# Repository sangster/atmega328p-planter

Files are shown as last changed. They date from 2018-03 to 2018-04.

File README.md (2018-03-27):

# Planter

This project manages the water and light cycles of a single houseplant.

This was a learning exercise to begin teaching myself embedded development. I
wouldn't recommend you use this code for anything you deem to be important.

For the sake of code-cleanliness, non-application code has been extracted to a
helper library:
[embedded-sangster_atmega328p](https://github.com/sangster/embedded-sangster_atmega328p).

## Features

 - An LCD screen which shows live statistics: Soil moisture, air humidity, air
   temperature, and the current date and time.
 - To save power, the LCD turns off 1 minute after the user stops pressing
   buttons.
 - A menu system which allows the user to change the runtime settings of the
   system (detailed below), using the four general-purpose buttons below the LCD
   screen.
 - Automatically waters the plant on a given schedule, but only if the soil
   moisture falls below a certain percentage.
 - An audible alarm system to notify you when the water tank runs low. This
   also disables the pump so it doesn't "run dry."
 - A toggle switch on the front panel to disable the audible alarm, in case it
   gets annoying.
 - Automatically turns on/off a grow light on a given schedule.
 - Supports an optional microSD card. If present, various spreadsheets will be
   populated over time. Hopefully, this data can be used to fine-tune your
   plant's care.

### Menu

The menu provides the following functionality and configuration options:

 - **Water Plant!**: Runs the watering process, regardless of the schedule or
   current soil moisture.
 - **Toggle Lamp**: Switches the lamp on/off, regardless of the current
   schedule. This "override" will continue until the next scheduled event. ex:
   If the lamp is scheduled to turn on at 8:00 am. If you toggle it off at 8:05
   am, it will remain off until 8:00 am the following day.
 - **Date Config**: Set the current year, month, and day.
 - **Time Config**: Set the current hour (24h clock) and minute.
 - **Lamp Config**:
   - **Starting hour**: The hour of the day the lamp should turn on.
   - **Period**: The number of hours the lamp should remain on.
 - **Pump Config**:
   - **Moisture Trigger**: The level of soil moisture (%) below which the pump
     will be allowed to run.
   - **Delay**: The minimum amount of time that must pass after watering the
     plant before watering it again.
   - **Amount**: The amount of water (mL) to water the plant with each time.
 - **Log Config**:
   - **Period**: How often general statistics will be written to the SD card
     (if one is available)

### Log Files

If the optional SD card is inserted, three types of log files (in the form of
.csv spreadsheets) will be populated over time.

#### General Statistics

Every so often (See the menu option **Log Config > Period**), the Planter will
dump all the statistics it has available to a log file. As this file will be
updated most often and has the most columns, a new file will be created each
month, with the filename format of `YYYY-MM.log`.

##### Example

| Time | Moisture (%) | Humidity (%) | Temperature (C) | Time of Last Watering | Conf: Lamp Start | Conf: Lamp Period (Hrs) | Conf: Pump Minimum (% Moisture) | Conf: Pump Delay (Hrs) | Conf: Pump Amount (mL) | Conf: Log Period (Mins) | Lamp State | Buoy State |
| --- | --- | --- | --- | --- | --- | --- | --- | --- | --- | --- | --- | --- |
| 2018-03-22 10:00:00 | 90 | 20 | 21 | 2018-03-21 20:31:59 | 08:00 | 10 | 20 | 4 | 50 | 6 | Off | Up |
| 2018-03-22 11:00:01 | 86 | 20 | 22 | 2018-03-21 20:31:59 | 08:00 | 10 | 20 | 4 | 50 | 6 | On | Up |

#### Watering History

Every time the plant gets watered a new entry is added to the `Water.log`
spreadsheet, including the soil moisture (%) before the plant was watered and
how much water was supplied.

##### Example

| Time | Moisture Before | mL |
| --- | --- | --- |
| 2018-03-12 00:12:17 | 19 | 52 |
| 2018-03-15 15:15:31 | 17 | 50 |

#### Watering History

Every time the grow light is turned on or off, the event is recorded in the
`Lamp.log` spreadsheet.

##### Example

| Time | New Lamp State |
| --- | --- |
| 2018-03-18 00:08:00 | On  |
| 2018-03-18 00:18:00 | Off |
| 2018-03-19 00:09:00 | On  |

## Build Process

### Major Components

  - Two custom PCBs (more info below):
    - Motherboard
    - UI panel
  - Generic 2x16 LCD panel
  - 4 momentary push buttons
  - 1 toggle switch
  - OSEPP Humidity & Moisture Breakout (MHUM-01)
  - OSEPP Real-time Clock & microSD Breakout (RTCSD-01)
  - Generic YF-S402 Water Flow Sensor
  - Water Level Sensor Vertical Float Switch
  - The cheapest, weakest DC acquarium pump you can find
  - A cheapo desk lamp, with a "grow" lightbulb
  - 12v/2amp AC adapter
  - 12cm x 12cm x 9cm plastic project box
  - A plastic container to act as the water resevoir

### Custom PCBs

This project uses 2 homemade PCBs to wire everything together:

 - The Motherboard
 - The UI panel daughterboard

Both were designed using the open-source [Fritzing](http://fritzing.org), then
etched onto copper clad using the "toner transfer" process.

#### Motherboard

The motherboard's responsibilities are:

 - Receive 12v from the AC adapter.
 - Step the power down to 5v for the MCU and various low voltage components.
 - Provide 12v to the pump (when active).
 - Switch the Lamp and Pump relays.
 - Provide headers to connect the UI panel and other peripheral components.

##### Files

 - [mainboard.fzz](./planning/mainboard.fzz): The Fritzing file used to design
   the PCB and print out the toner-transfer sheets.
 - [mainboard.pdf](./toner-transfers/mainboard.pdf): The sheet to print to the
   transparency sheet, used for the transfer process. There are multiple copies
   per sheet, to allow for mistakes.

#### UI Panel

The UI Panel's responsibilities are:

 - Attaching to the lid of the project box.
 - Hosting buttons on one side, to be pushed through holes in the lid, and
   internal connects on the reverse side.
 - Providing headers to connect the LCD screen, also attached to box's lid.
 - Providing headers to connect to the alarm mute switch, also attache to the
   box's lid.
 - Provide a trimmer to adjust the LCD backlight

##### Files

 - [ui-panel.fzz](./planning/ui-panel.fzz): The Fritzing file used to design
   the PCB and print out the toner-transfer sheets.
 - [ui-panel.pdf](./toner-transfers/ui-panel.pdf): The sheet to print to the
   transparency sheet, used for the transfer process. There are multiple copies
   per sheet, to allow for mistakes.

### Assembly

The open-source [OpenSCAD](http://www.openscad.org/) CAD modelling tool was used
to determine where each component would be physicall located within the project
box. These files are held in the [cad/](./cad/) directory, but the main file is
[assembly.scad](./cad/assembly.scad).

OpenSCAD is also use for printing out the pattern of holes you need to cut out
of the project box to make room for buttons/LCD/etc by printing a 2D project of
the 3D model.

### Photos

Because this project is to create an actual device, photos should help. Please
keep in mind that this is my first embedded device. :)

How the project started: an empty plastic box and a "mockup" of the major
components on a breadboard.

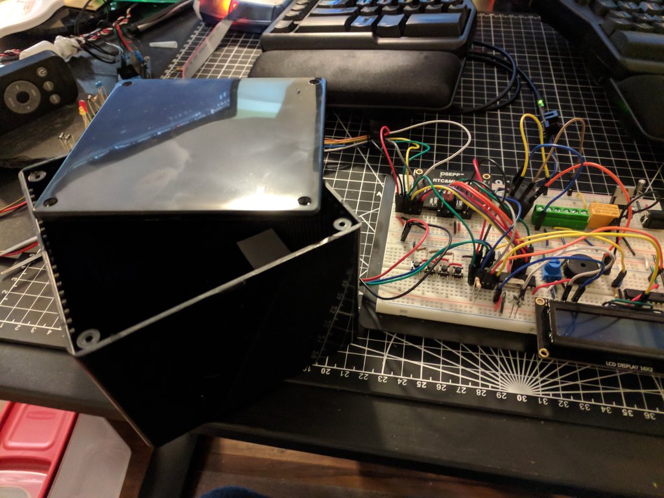
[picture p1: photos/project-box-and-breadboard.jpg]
The project box next to the breadboard version


---

The homebrew motherboard. The relays switch the pump and lamp. The LM7805
voltage regulator (right side of the image) bringe the 12v (required for the
pump) down to 5v (required for the MCU and other components).

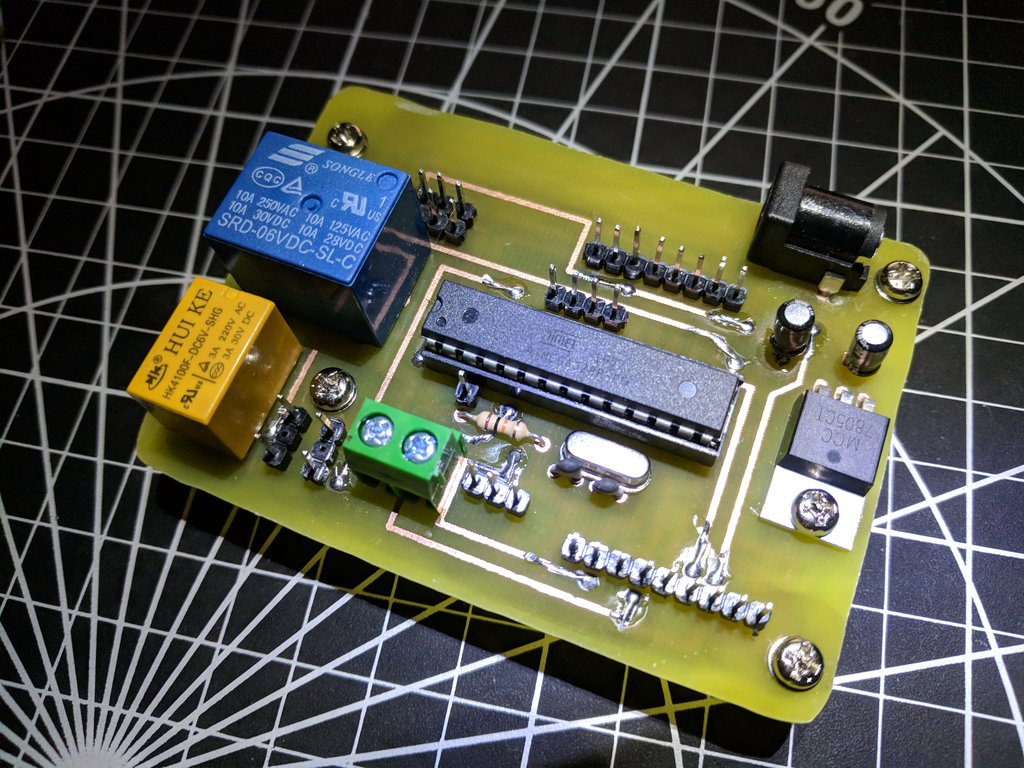
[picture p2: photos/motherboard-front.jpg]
Motherboard PCB: front

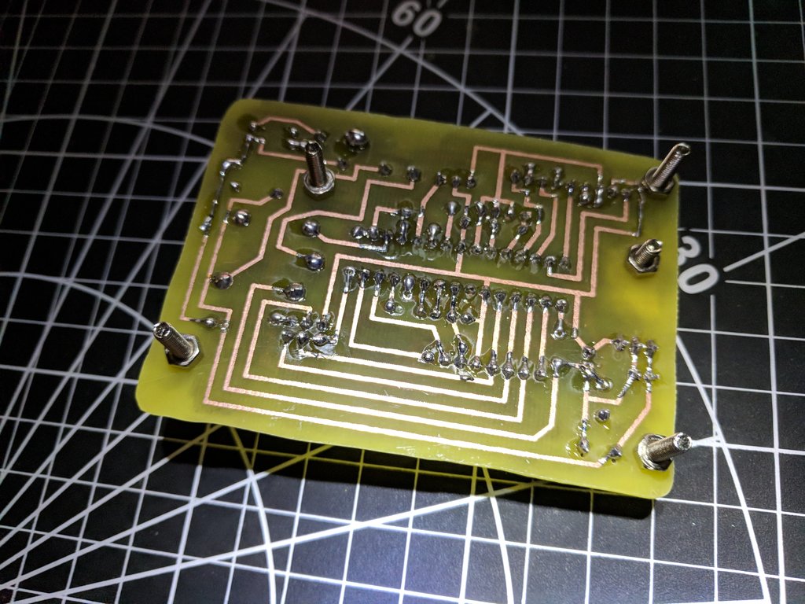
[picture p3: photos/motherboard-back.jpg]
Motherboard PCB: back


---

The components mounted to the box itself: the 12v AC adapter, motherboard,
SD/RTC breakout board, and flow sensor.

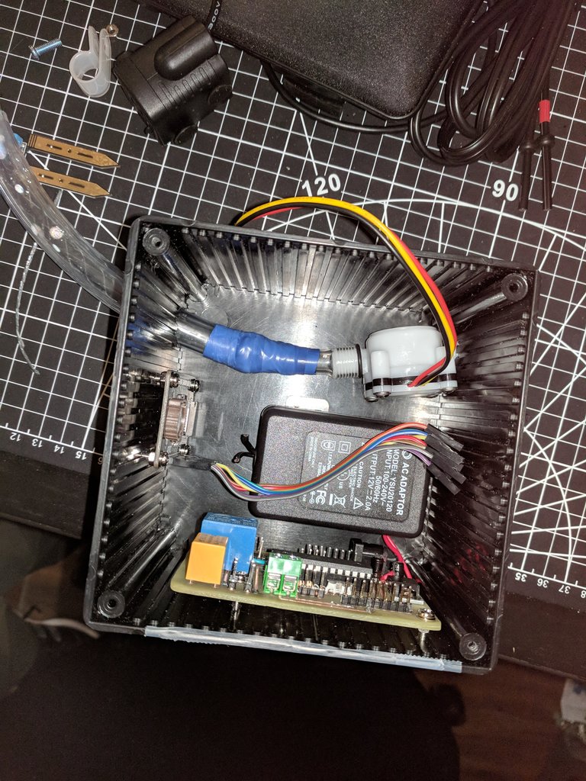
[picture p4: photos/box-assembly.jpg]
Internal components, without lid


---

The UI panel PCB. You can see the buttons alone are on the front side. This is
so they can be pushed through holes cut in the lid. The remaining components
are on the back, so the front can remain as flat as possible.

On the back there is the LCD backlight trimmer, water-low-alarm buzzer, and LCD
shift register (drives the LCD with 2 pins instead of 4)

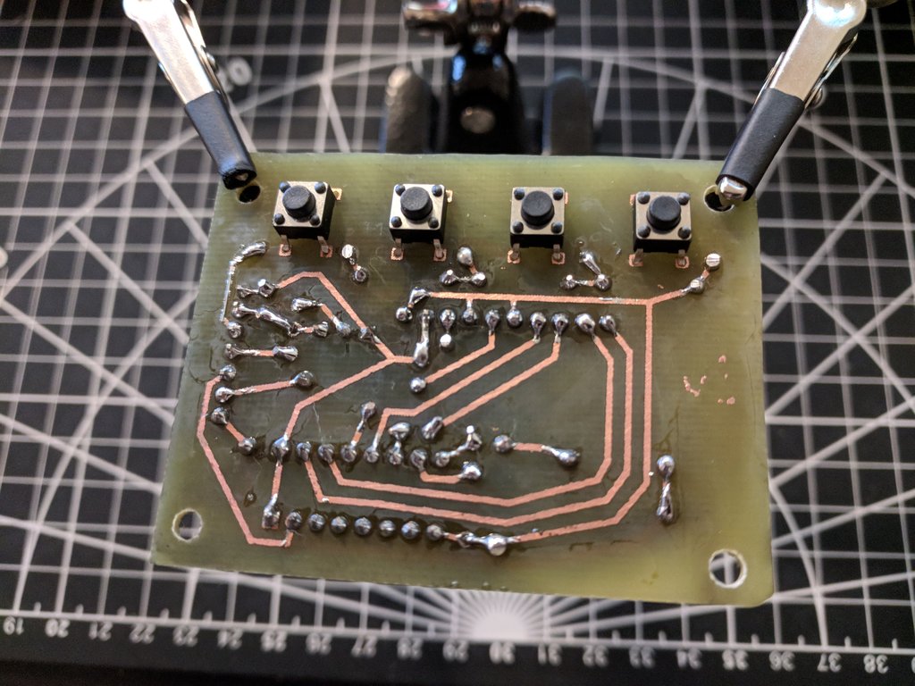
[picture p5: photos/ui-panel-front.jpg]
UI Panel PCB: front

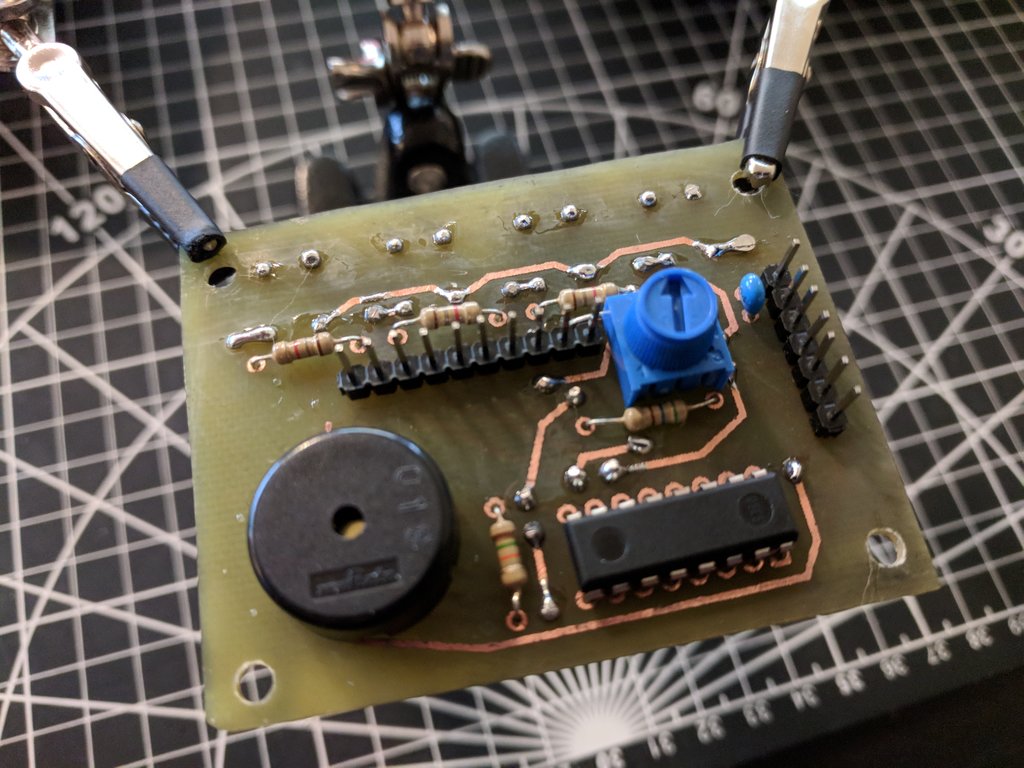
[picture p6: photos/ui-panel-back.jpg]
UI Panel PCB: back


---

The assembled lid. OpenSCAD provided the template used to cut out holes in the
lid. The alignment was pretty critial to ensure the buttons on the PCB ligned
up with the holes, as well as their icons on the LCD display. Also featured:
the alarm mute switch.

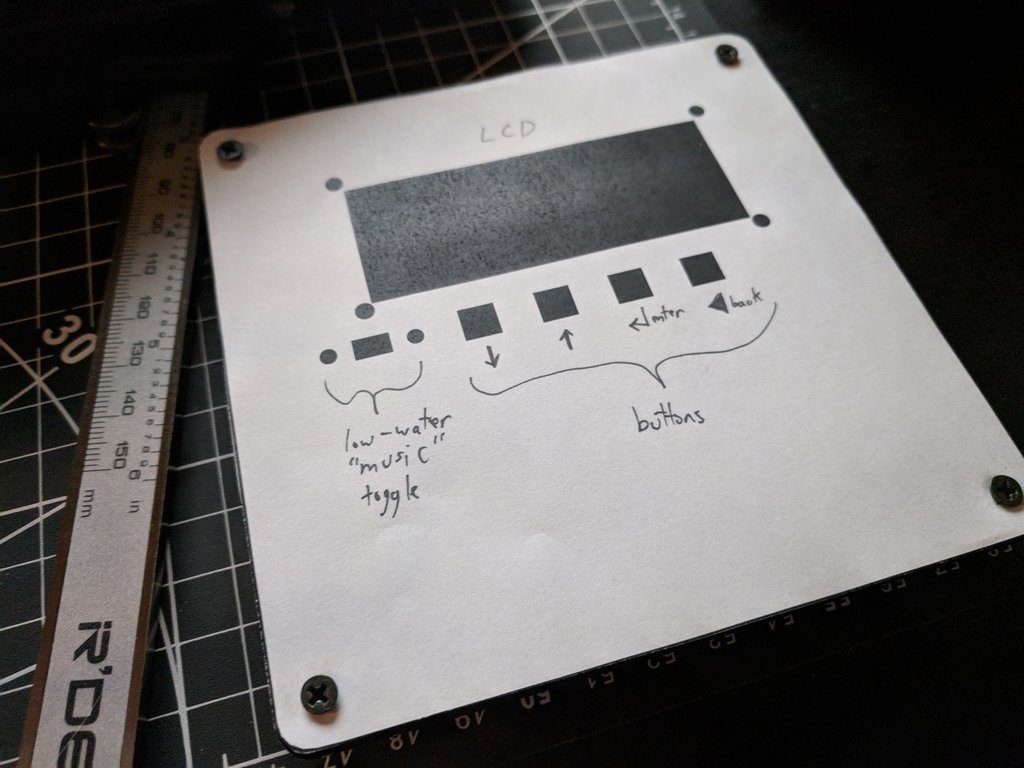
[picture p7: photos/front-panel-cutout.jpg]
Template of holes to cut out of front panel

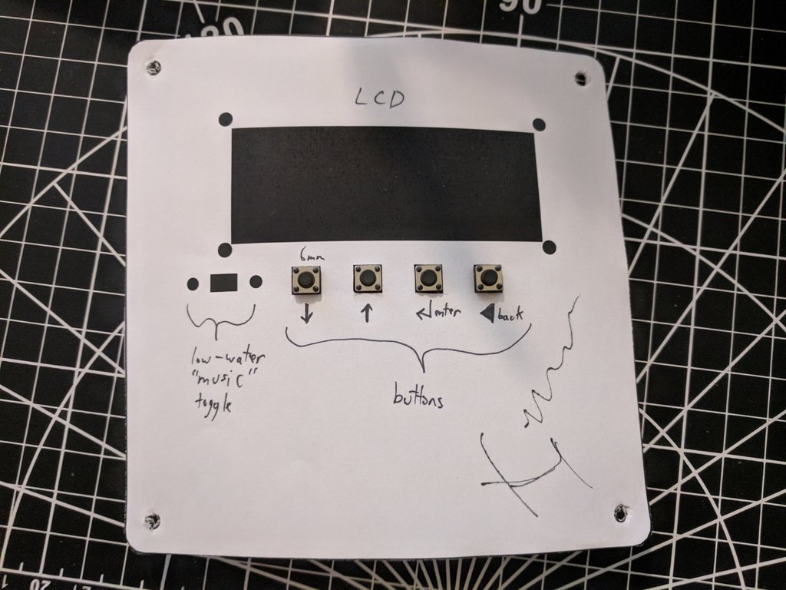
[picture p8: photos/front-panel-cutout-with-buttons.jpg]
Template showing the buttons are correctly spaced


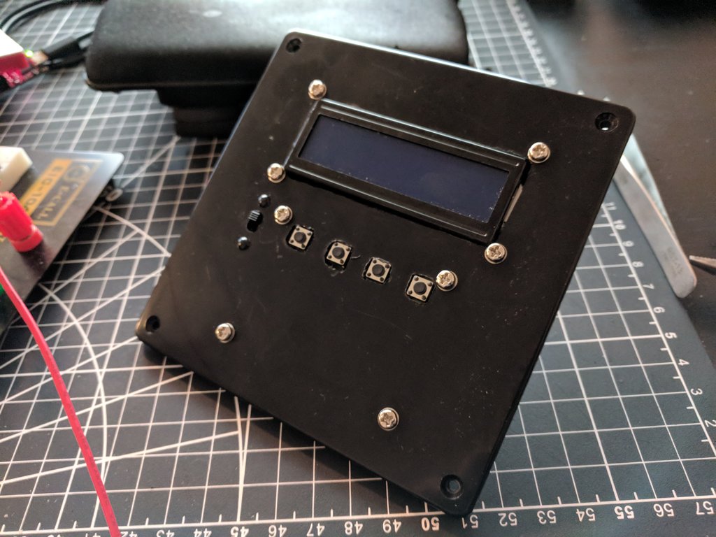
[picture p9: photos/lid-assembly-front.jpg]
Assembled UI panel: front

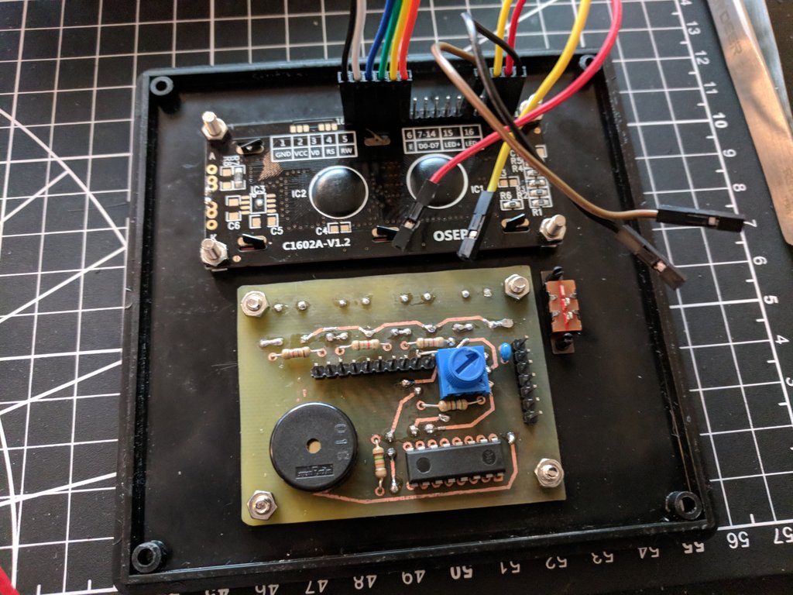
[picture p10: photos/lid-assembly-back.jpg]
Assembled UI panel: back


---

Final assembly was simply plugging in all the wires to their correct headers.

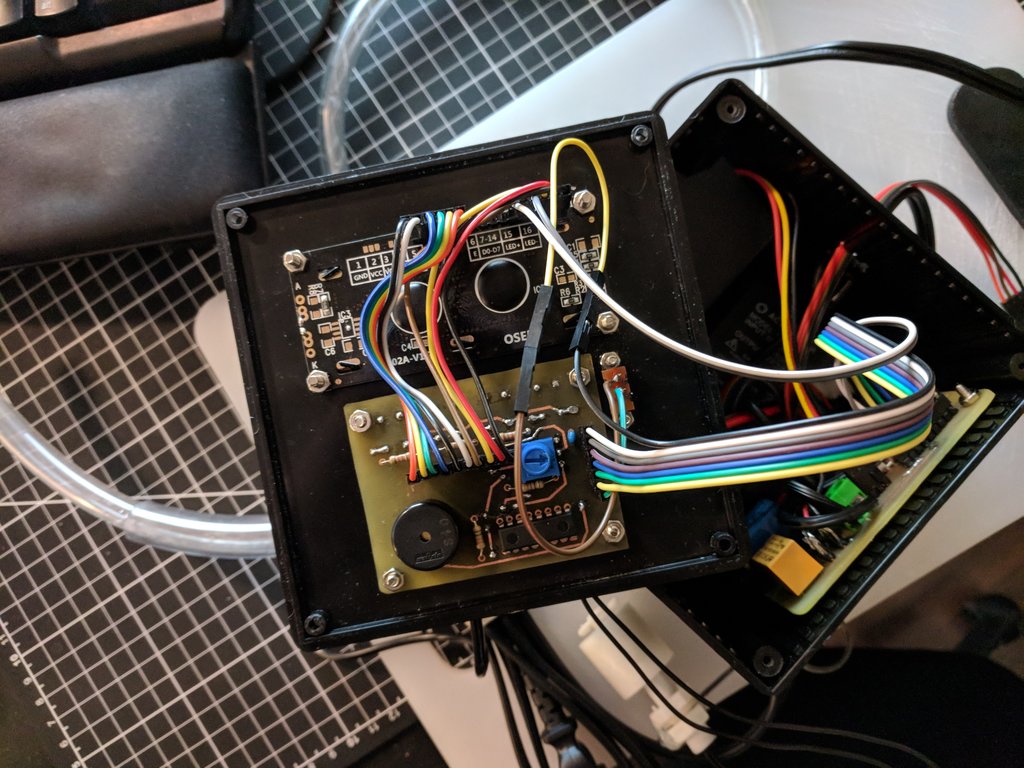
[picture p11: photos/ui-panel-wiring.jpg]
UI Panel: wired to LCB and motherboard

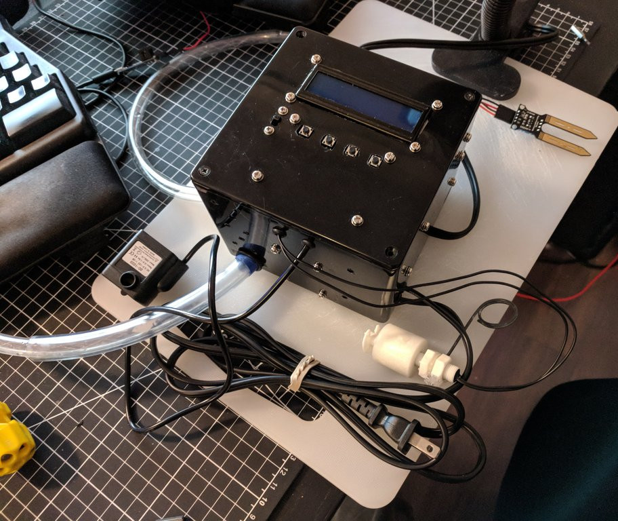
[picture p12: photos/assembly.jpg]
Assembled Project


---

And the initial test run. You can see the probe in the soil and the pump/float
system in the water resevoir. The project is quite light, so I just screwed it
to the top of the resevoir. Also featured: a bonsai tree near death from
waiting for this project's completion.

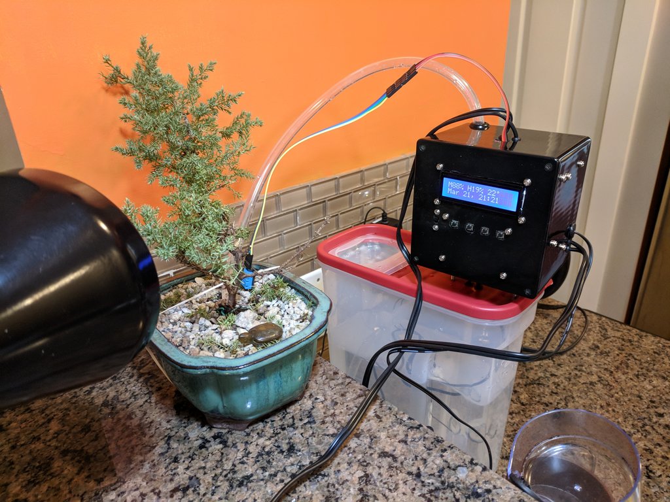
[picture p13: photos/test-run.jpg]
The first test run of the system

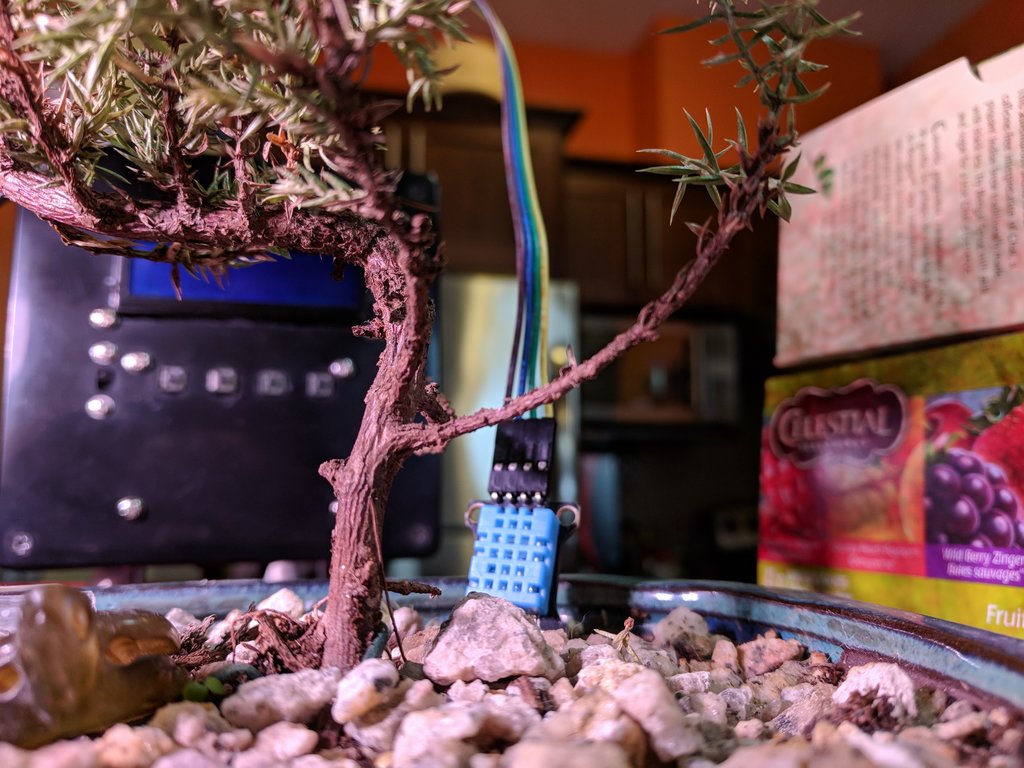
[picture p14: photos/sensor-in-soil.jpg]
Humidity/Moisture/Temperature probe in the soil

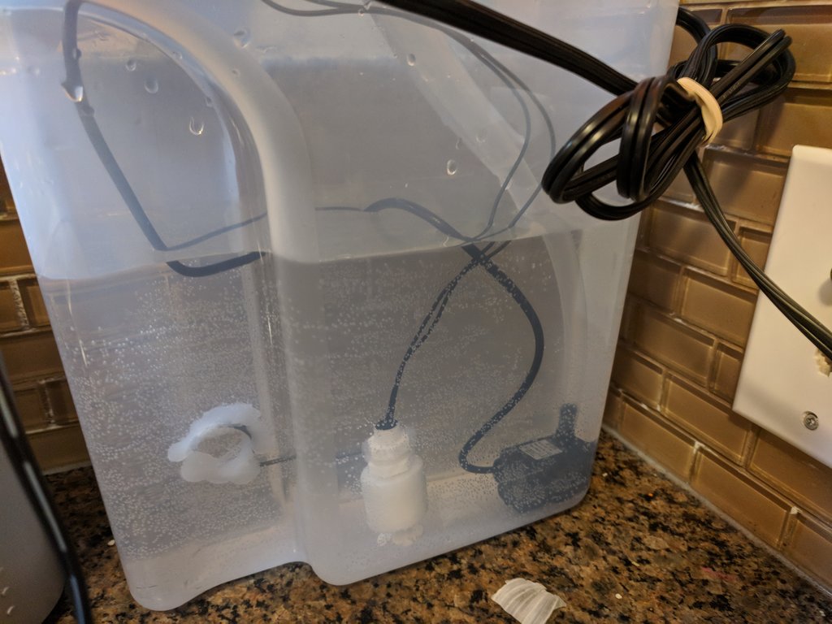
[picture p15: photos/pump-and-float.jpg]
The pump and float in the water resevoir


---

## Deployment

Uploading the code to the microcontroller should be as simple as:

```sh
make upload
```

## License

This project is licensed under the GPL License - see the [LICENSE](./LICENSE)
file for details

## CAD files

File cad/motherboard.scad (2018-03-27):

/*
 *  "Planter" is a device that control a houseplant's water and light schedules.
 *  Copyright (C) 2018  Jon Sangster
 *
 *  This program is free software: you can redistribute it and/or modify it
 *  under the terms of the GNU General Public License as published by the Free
 *  Software Foundation, either version 3 of the License, or (at your option)
 *  any later version.
 *
 *  This program is distributed in the hope that it will be useful, but WITHOUT
 *  ANY WARRANTY; without even the implied warranty of MERCHANTABILITY or
 *  FITNESS FOR A PARTICULAR PURPOSE.  See the GNU General Public License for
 *  more details.
 *
 *  You should have received a copy of the GNU General Public License along
 *  with this program.  If not, see <https://www.gnu.org/licenses/>.
 */
include <motherboard_vars.scad>;

module motherboard(part = "positive")
{
    if (part == "negative") {
        motherboard_pcb_holes();
    } else {
        _motherboard();
    }
}


module _motherboard()
{
    difference() {
        color("Wheat") cube([mb_x, mb_y, mb_z]);
        motherboard_pcb_holes();
    }
}


module motherboard_pcb_holes()
{
    translate([0, 0, -mb_z]) {
        for (location = mb_pcb_holes) {
            translate(location) {
                translate([-mb_pcb_hole_d/2, -mb_pcb_hole_d/2]) {
                    cylinder(d = mb_pcb_hole_d, h = mb_pcb_hole_z, $fn = 32);
                 }
            }
        }
    }
}

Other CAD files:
cad/motherboard_vars.scad
cad/assembly.scad
cad/box-assembly.scad
cad/box.scad
cad/box_vars.scad
cad/button.scad
cad/button_vars.scad
cad/flow.scad
cad/flow_vars.scad
cad/lcd.scad
cad/lcd_vars.scad
cad/lid-assembly.scad
cad/power.scad
cad/power_vars.scad
cad/rtc.scad
cad/rtc_vars.scad
cad/switch.scad
cad/switch_vars.scad
cad/ui-pcb.scad
cad/ui-pcb_vars.scad

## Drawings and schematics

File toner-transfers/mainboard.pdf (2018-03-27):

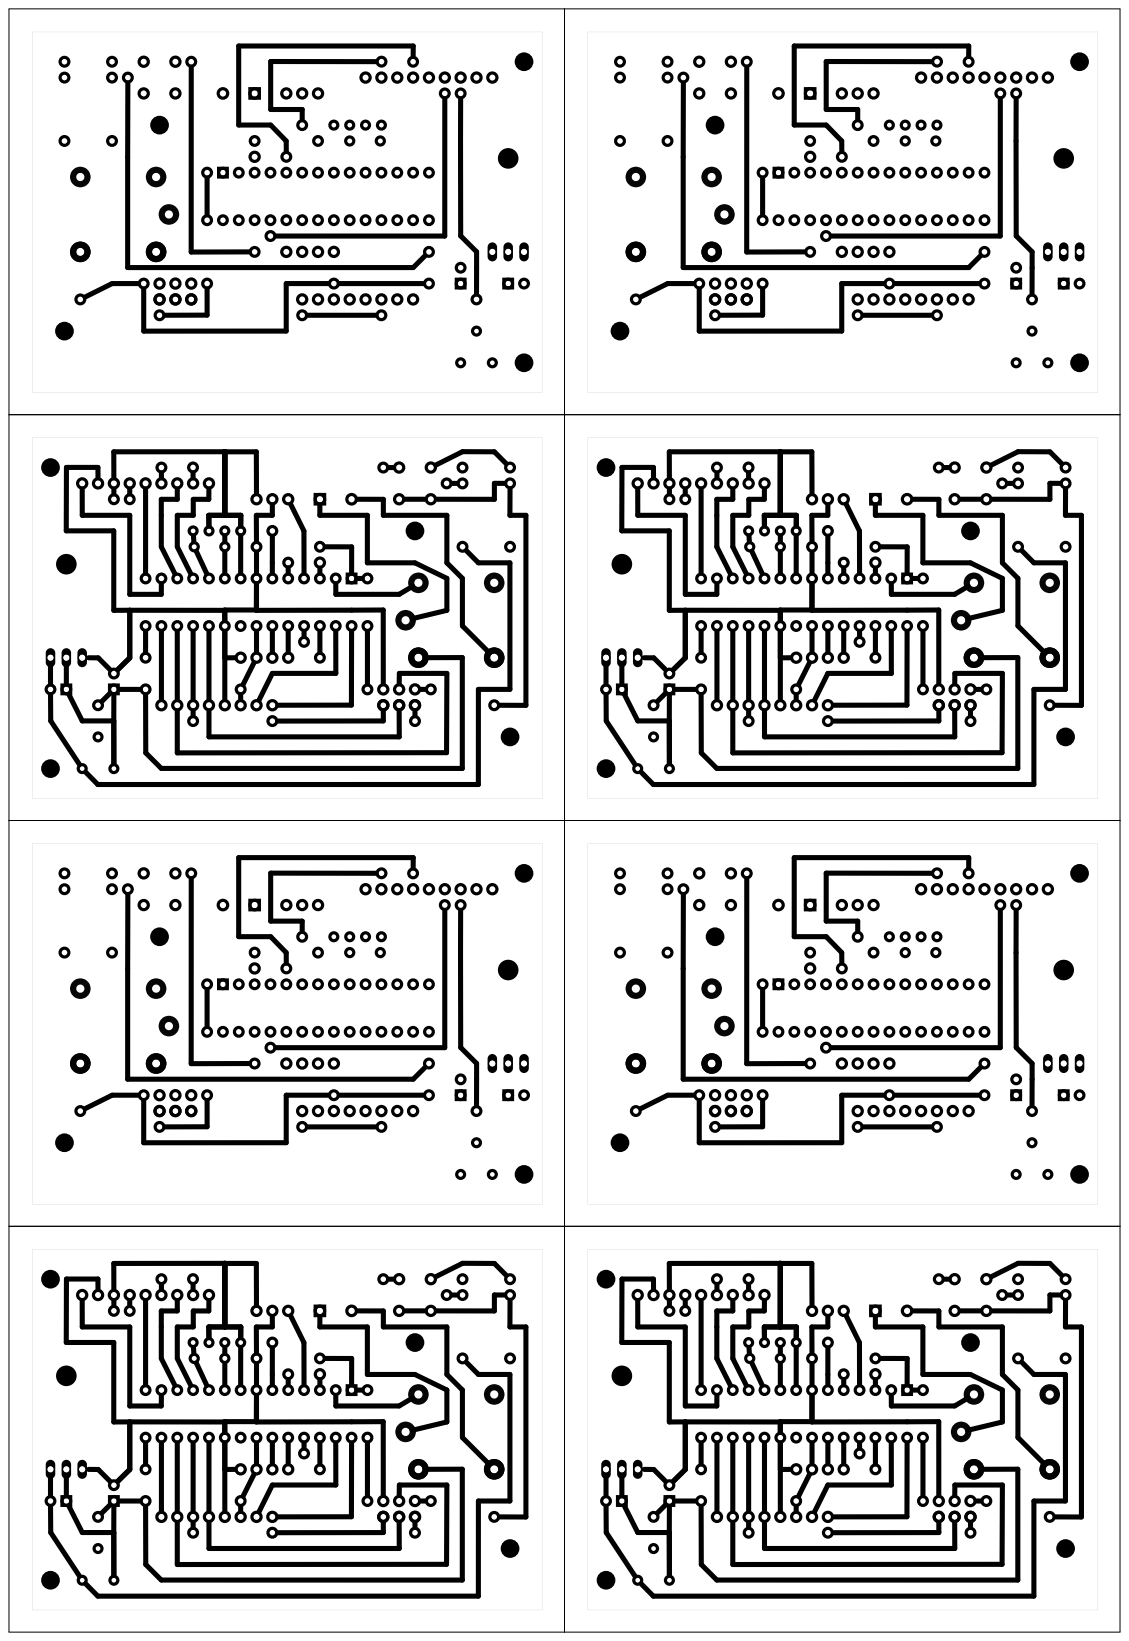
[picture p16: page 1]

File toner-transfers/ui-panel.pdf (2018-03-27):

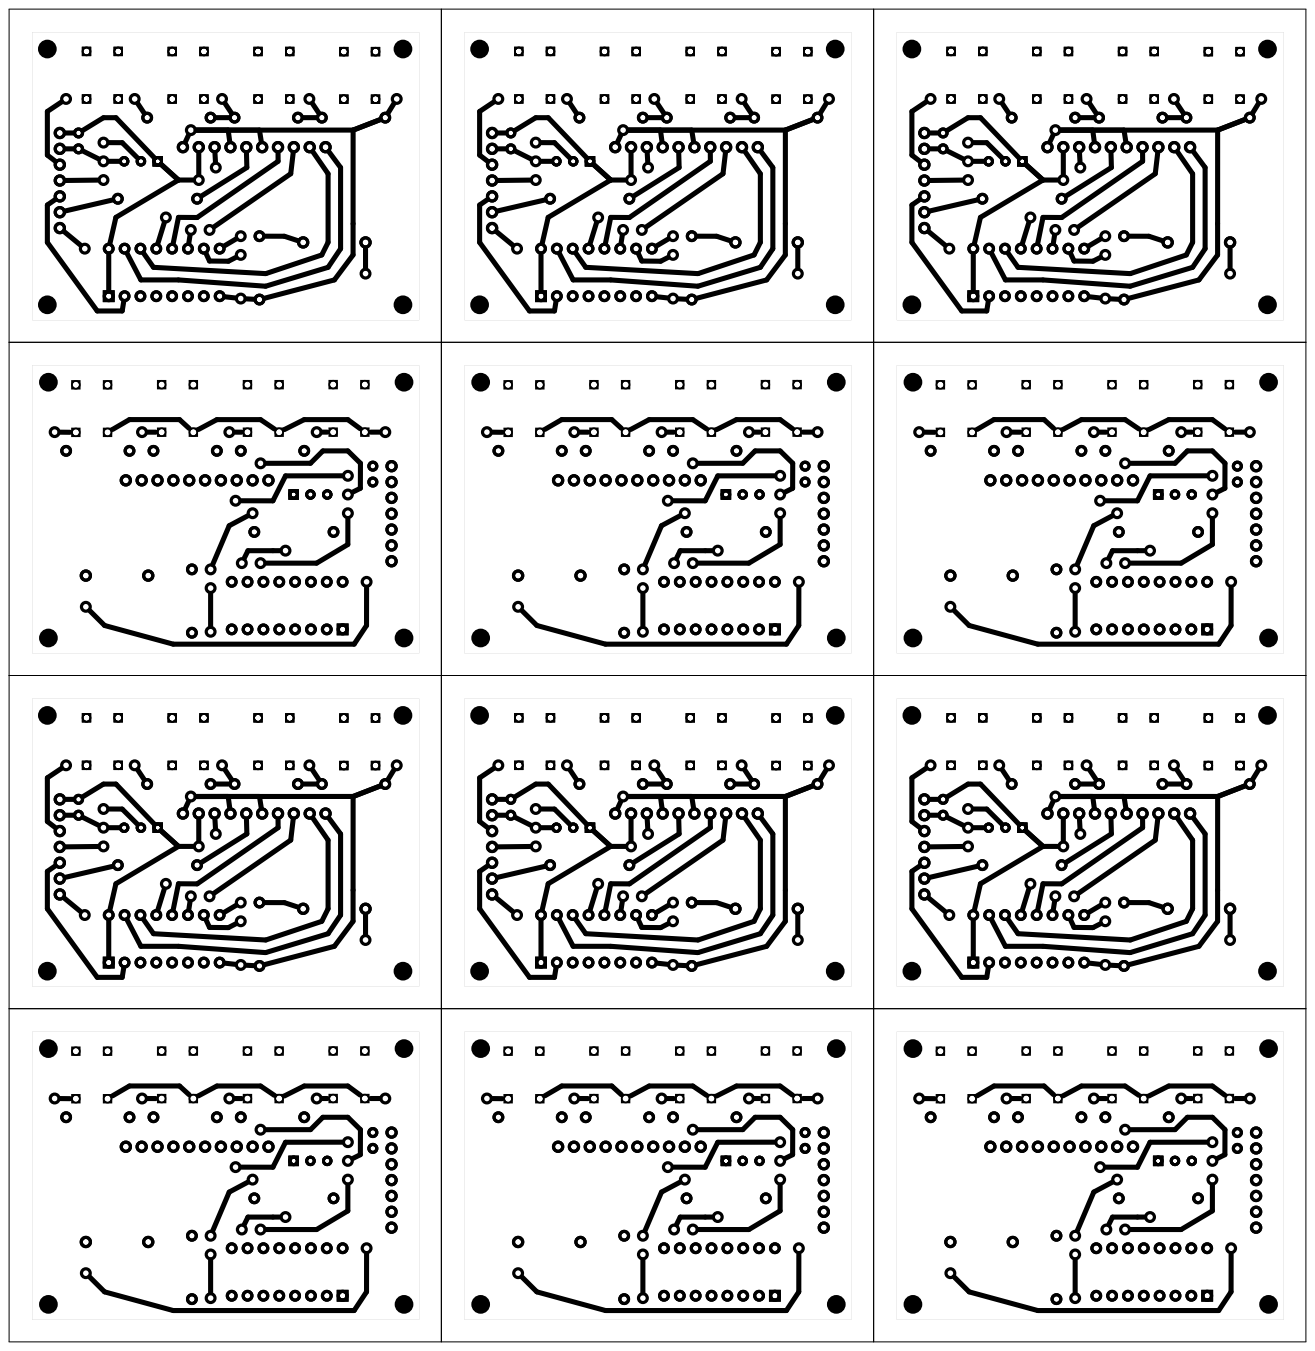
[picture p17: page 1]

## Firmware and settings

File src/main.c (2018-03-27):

/* @file
 *
 *  "Planter" is a device that control a houseplant's water and light schedules.
 *  Copyright (C) 2018  Jon Sangster
 *
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
 *  You should have received a copy of the GNU General Public License along
 *  with this program.  If not, see <https://www.gnu.org/licenses/>.
 */
#include <stdbool.h>
#include <time.h>
#include <avr/interrupt.h>
#include <avr/io.h>
#include <avr/pgmspace.h>
#include <util/delay.h>
#include <sangster/lcd.h>
#include <sangster/pinout.h>
#include <sangster/ring_buff_8.h>
#include <sangster/rtc_1307.h>
#include <sangster/sd.h>
#include <sangster/timer0.h>
#include <sangster/twi.h>
#include <sangster/usart.h>
#include <sangster/usart_p.h>

#include "buzzer.h"
#include "log.h"
#include "menu.h"
#include "pump.h"
#include "rtc.h"
#include "sensors.h"
#include "settings.h"


/*******************************************************************************
 * Constants
 ******************************************************************************/
/**
 * How long to keep the LCD screen on (in seconds) after the user's keypress.
 */
#define SCREEN_TIMEOUT  60

/**
 * How long to wait (in seconds) to check if the plant needs water after
 * booting. When we start up, we don't know how long it's been since the plant
 * was last watered, so we probably don't want to wait until the next normally
 * scheduled time.
 */
#define STARTUP_PUMP_CHECK_TIME  10 * 60 // seconds

/**
 * How long to wait (in seconds) before writing to the log immediately after
 * booting. It may be useful to capture stats shortly after starting up, so we
 * don't want to wait unti the normal log schedule.
 */
#define STARTUP_LOG_TIME  2 * 60

/**
 * The timezone offset (seconds) use when creating file timestanps on the SD
 * card.
 */
#define SD_TIMEZONE_OFFSET  -8 * 3600

/**
 * To avoid over-taxing some of the sensors, we only poll them every so many ms.
 */
#define CHECK_SYSTEM_MS  250

/**
 * The Moisture/Humidity/Temperature is even slower than other sensors and can
 * only be polled once per second.
 */
#define CHECK_MHUM_MS   1000

/**
 * Calculate the number of clock cycles required to ensure `TIMER1` overflows
 * after #CHECK_SYSTEM_MS milliseconds.
 *
 * @note At 16 MHz, 1 second == (62500 * 256) / 16e6 cycles
 */
#define SENSOR_CLKS  (62500 / (1000 / CHECK_SYSTEM_MS))


/** A 16 character splash-screen to show when booting up.  */
PROGMEM const char APP_TITLE[] = "Planter     v1.0";

/** The root diretory on the SD card in which to place all the log files.  */
PROGMEM const char SD_DIR[] = "Plant1_0";


/*******************************************************************************
 * Functions
 ******************************************************************************/
__attribute__((always_inline)) inline void setup();
__attribute__((always_inline)) inline void loop();
__attribute__((always_inline)) inline void handle_ui();
__attribute__((always_inline)) inline void show_status_on_lcd();

void setup_pump();
void setup_lcd();
void setup_rtc();
void setup_buzzer();
void setup_buttons();
void setup_sd();

void read_sensors();
void check_lamp();
void toggle_lamp();
void set_lamp_enabled(bool);
void check_pump();
void start_pump();
void set_lcd_enabled(bool);
void check_log();

void menu_edit_date_callback(struct tm);
void menu_edit_settings_callback(Settings);
void menu_function_dispatch(MenuMode);
void shift_lcd_write4(const Lcd*, const uint8_t nibble);
void on_water_level_change(BuoyLevel);
void sd_set_file_date_time(uint16_t* date, uint16_t* time);

void fatal_error_P(const char*, const char*);


/*******************************************************************************
 * Pins
 ******************************************************************************/
// See Table 28-4 in the ATMega328p manual
#define PIN_BUTTONS_MUX  _BV(MUX1) // ADC2
#define PIN_MOIST_MUX            0 // ADC0

// Input
const Pinout pin_buoy    = {&PORTC, PORTC3}; ///< Buoy sensor
const Pinout pin_humid   = {&PORTC, PORTC1}; ///< Humidity sensor
const Pinout pin_moist   = {&PORTC, PORTC0}; ///< Moisture/Temperature sensor
const Pinout pin_buttons = {&PORTC, PORTC2}; ///< Buttons sensor
const Pinout pin_flow    = {&PORTD, PORTD2}; ///< Water flow sensor
                                             ///< only used for INT0 interupt!

// Output
const Pinout pin_pump = {&PORTB, PORTB1};          ///< Pump output
const Pinout pin_lamp = {&PORTD, PORTD0};          ///< Lamp output
const Pinout pin_buzz = {&PORTD, PORTD7};          ///< Buzzer output
const Pinout pin_lcd_data = {&PORTD, PORTD3};      ///< LCD data output
const Pinout pin_lcd_clk  = {&PORTB, PORTB0};      ///< LCD clock output
const Pinout pin_lcd_backlight = {&PORTD, PORTD6}; ///< LCD backlight switch


/** LCD breakout board */
Lcd lcd = {
    .rs = {&PORTD, PORTD5},
    .en = {&PORTD, PORTD4},
};

bool sd_card_available = false;
SdFile log_dir;

/** SD Card breakout board */
SdClass SD = {
    .card = {
        .chip_select_pin = {&PORTB, PORTB2},
        .mosi_pin        = {&PORTB, PORTB3},
        .miso_pin        = {&PORTB, PORTB4},
        .clock_pin       = {&PORTB, PORTB5},
    }
};

/** Realtime Clock breakout board */
Rtc1307 rtc = {
    .twi = {
        .pin_sda = {&PORTC, PORTC4},
        .pin_scl = {&PORTC, PORTC5},
    }
};


/*******************************************************************************
 * State
 ******************************************************************************/
bool fatal_error_active = false;
char fatal_error_lcd0[16];
char fatal_error_lcd1[16];

uint8_t check_system_counter = 0;
volatile bool recheck_scheduled = false;

Settings settings;
struct tm current_time;

uint8_t moisture_before_pumping = 0;

bool lamp_override = false;
bool lamp_override_on = false;

char lcd_buffer[LCD_ROWS][LCD_COLS];
struct tm lcd_timeout_at;
bool lcd_is_on = false;

RING_BUFF_8_DEF(moisture, 4);
RING_BUFF_8_DEF(humidity, 4);
RING_BUFF_8_DEF(temperature, 4);


/*******************************************************************************
 * Interrupts
 ******************************************************************************/
ISR(INT0_vect)
{
    pump_flow_callback(); // counts flow sensor frequency
}

ISR(TIMER0_OVF_vect)
{
    timer0_interrupt_callback();
}

ISR(TIMER1_COMPA_vect)
{
    recheck_scheduled = true;
}

ISR(TIMER2_COMPA_vect)
{
    pinout_toggle(pin_buzz); // Creates the tone frequency when the buzzer is on
}

ISR(TWI_vect)
{
    twi_handle_vect(); // Handle communication from the RTC's TWI interface
}


/*******************************************************************************
 * Main Program
 ******************************************************************************/

__attribute__((OS_main))
int main(void)
{
    // Usart for console logging/debugging
    usart_init(9600, FORMAT_8N1);
    UCSR0B |= _BV(TXEN0);
    usart_println_P(APP_TITLE);

    setup();
    for(;;) {
        loop(); // TODO: is this really inline?
    }
}


/**
 * @defgroup Setup Setup function
 */
/// @{
void setup()
{
    pinout_make_input(pin_flow);
    pinout_make_pullup_input(pin_buoy);
    pinout_make_pullup_input(pin_humid);
    pinout_make_pullup_input(pin_buttons); // max value == no buttons clicked

    pinout_make_output(pin_pump);
    pinout_make_output(pin_lamp);
    pinout_make_output(lcd.rs);
    pinout_make_output(lcd.en);
    pinout_make_output(pin_lcd_data);
    pinout_make_output(pin_lcd_clk);
    pinout_make_output(pin_lcd_backlight);
    pinout_make_output(pin_buzz);

    restore_settings_from_eeprom(&settings);

    sei();

    // Setup devices
    setup_pump();
    setup_lcd();
    lcd_buffer_update_P(&lcd, 0, APP_TITLE);
    setup_rtc();
    setup_buzzer();
    setup_buttons();

    // Start system check timer
    OCR1A = SENSOR_CLKS;
    TCCR1B |= _BV(WGM12) | _BV(CS12); // CTC mode, 256 prescaler
    TIMSK1 |= _BV(OCIE1A);

    read_sensors();

    // Setup SD Card
    setup_sd();
    usart_println_P(sd_card_available ? PSTR("mounted") : PSTR("ejected"));

    // avoid pumping immediately
    time_t last_pump = mk_gmtime(&current_time) - settings.pump_delay * 3600
                           + STARTUP_PUMP_CHECK_TIME;
    gmtime_r(&last_pump, &pump_last_time);

    // avoid logging immediately
    time_t last_log = mk_gmtime(&current_time) - log_period_seconds(settings.log_period)
                           + STARTUP_LOG_TIME;
    gmtime_r(&last_log, &log_last_time);

    set_lcd_enabled(true); // enable the UI!
}


void setup_pump()
{
    // INT0, falling edge
    PIND |= _BV(pin_flow.pin); // enable pullup on INT0 pin
    EIMSK |= _BV(INT0);
    EICRA |= _BV(ISC01);
}


void setup_lcd()
{
    pinout_set(pin_lcd_backlight);

    lcd.back_buffer = &lcd_buffer;
    lcd_init(&lcd, 2, shift_lcd_write4);
}


void setup_rtc()
{
    if (!rtc_init(&rtc)) {
        usart_println_P(PSTR("RTC init error"));
        fatal_error_P(PSTR("RTC init error"), PSTR(""));
    }
}


void setup_buzzer()
{
    TCCR2A |= _BV(WGM21);  // Mode CTC: OCRA
}


void setup_buttons()
{
    ADMUX |= _BV(REFS0) | (PIN_BUTTONS_MUX);  // AVcc <- external capacitor
    ADCSRA |= _BV(ADPS2) | _BV(ADPS1);        // Prescaler: 64
    ADCSRA |= _BV(ADEN);                      // Enable ADC
}


void setup_sd()
{
    usart_print_P(PSTR("Init SD card... "));
    if (!sd_begin(&SD, sd_set_file_date_time)) {
        char num_str[4];

        sd_card_available = false;

        usart_print_P(PSTR("SD CARD init failure: "));
        usart_dump_array_8(&(SD.card.error_code), 1);

        lcd_buffer_update_P(&lcd, 0, PSTR("SD Card Failure"));
        lcd_buffer_update_P(&lcd, 1, PSTR("error code: "));

        itoa(SD.card.error_code, num_str, 10);
        lcd_buffer_update_at(&lcd, 1, 11, num_str);

        _delay_ms(10000);
        return;
    }

    // Open logging directory
    char path[12];
    strncpy_P(path, SD_DIR, 11);

    sd_mkdir(&SD, path);
    log_dir = sd_open(&SD, path, O_READ);
    sd_file_sync(&log_dir);

    sd_card_available = true;
}

/// @}


/**
 * The application's main loop
 */
void loop()
{
    if (fatal_error_active) {
        lcd_buffer_update(&lcd, 0, fatal_error_lcd0);
        lcd_buffer_update(&lcd, 1, fatal_error_lcd1);
    } else {
        if (recheck_scheduled) {
            recheck_scheduled = false;

            if (pinout_is_clr(pin_pump)) {
                read_sensors();
                check_lamp();

                if (sd_card_available) {
                    check_log();
                }
            }
            check_pump();
        }

        if (pinout_is_set(pin_pump)) {
            lcd_buffer_update_P(&lcd, 0, PSTR("    Pumping!"));
            lcd_buffer_update_P(&lcd, 1, PSTR("  Please Wait  "));
        } else {
            handle_ui();
        }
    }
    // vvv Regardless of Error state vvv

    if (buzzer_is_on) {
        buzzer_sound(pin_buzz);
    }
}


/**
 * Read the current value from our sensors:
 *
 *  - RTC time
 *  - Buoyancy (water level)
 *  - Moisture
 *  - Humidity
 *  - Temperature
 */
void read_sensors()
{
    // The DHT11 moisture/humidity sensor can only be checked every second, so
    // we only read it every N cycles.
    static uint8_t mhum_cycle = 0;

    rtc_read(&current_time);

    read_buoyancy(pin_buoy, &on_water_level_change);
    read_moisture(PIN_MOIST_MUX, &moisture);

    if (mhum_cycle == (CHECK_MHUM_MS / CHECK_SYSTEM_MS - 1) &&
        !read_humidity_temperature(pin_humid, &humidity, &temperature)) {
        usart_println_P(PSTR("Error reading MHUM-01"));
    }
    mhum_cycle = (mhum_cycle + 1) % (CHECK_MHUM_MS / CHECK_SYSTEM_MS);
}


void check_lamp()
{
    uint8_t curr  = current_time.tm_hour,
            start = settings.lamp_start,
            end   = (start + settings.lamp_period) % 24;

    if (lamp_override) {
        // The user forced the lamp on/off, but we only honor this until the
        // next start/stop time in the lamp's schedule.
        if (lamp_override_on && curr == end) {
            set_lamp_enabled(false);
            lamp_override = false;
        } else if (!lamp_override_on && curr == start) {
            set_lamp_enabled(true);
            lamp_override = false;
        }
    } else {
        if (end > start) {
            // lamp scheduled to turn on then off in the same calendar day
            set_lamp_enabled(curr >= start && curr < end);
        } else {
            // lamp scheduled to turn on one day then off after midnight
            set_lamp_enabled(curr >= start || curr < end);
        }
    }
}


/*
 * If the pump is currently running, check if it has pumped enough water yet
 * and stop it. If it isn't running, check if it's scheduled watering time has
 * arrived.
 */
void check_pump()
{
    if (pinout_is_set(pin_pump)) {
        int16_t total_ml = pump_check(pin_pump, &settings, buoy_state);

        switch(total_ml) {
            case PUMP_STATUS_PUMPING:
                break;
            case PUMP_STATUS_UNPLUGGED:
                fatal_error_P(PSTR("  Flow Sensor"),
                              PSTR("  Unplugged!"));
                break;
            default:
                if (sd_card_available) {
                    log_pump(&log_dir, current_time, total_ml,
                             moisture_before_pumping);
                } else {
                    usart_println_P(PSTR("SD unavailable. Cannot log pump."));
                }
                break;
        }

    } else {
        uint16_t delay = settings.pump_delay * 3600;
        int32_t time_until_pump = difftime(mk_gmtime(&pump_last_time) + delay,
                                            mk_gmtime(&current_time));

        if (time_until_pump <= 0) {
            pump_last_time = current_time;

            if (buoy_state == BUOY_UP) {
                if (ring_buff_8_avg(&moisture) <= settings.pump_min) {
                    pump_start(pin_pump);
                }
            }
        }
    }
}


void start_pump()
{
    moisture_before_pumping = ring_buff_8_avg(&moisture);
    pump_start(pin_pump);
}


void toggle_lamp()
{
    set_lamp_enabled(pinout_is_clr(pin_lamp));
}


/*
 * Respond to key presses and display the correct screen to the user.
 */
void handle_ui()
{
    const KeyCode key = keycode(PIN_BUTTONS_MUX);

    // Turn on LCD
    if (key != KEY_NONE) {
        bool lcd_was_off = !lcd_is_on;
        set_lcd_enabled(true);
        if (lcd_was_off) {
            return; // turning on the screen has consumed this keypress
        }
    }

    // turrn off LCD, if inactive
    const int32_t time_left = difftime(mk_gmtime(&lcd_timeout_at),
                                       mk_gmtime(&current_time));
    if (time_left <= 0) {
        set_lcd_enabled(false);
    }
    if (!lcd_is_on) {
        return; // User is AFK
    }

    switch (current_mode) {
        case SHOW_STATUS:
            if (key) {
                current_mode = SELECT_MENU;
                current_menu_mode = MENU_MODE_FIRST;
            }

            show_status_on_lcd();
            break;

        case SELECT_MENU:
            handle_menu_select(&lcd, key, &menu_function_dispatch);
            break;

        case EDIT_MENU:
            handle_menu_edit(&lcd, key, menu_edit_date_callback,
                             menu_edit_settings_callback);
            break;
    }
}


/*
 * Respond to the user choosing a new date or time via the menu.
 */
void menu_edit_date_callback(struct tm new)
{
    int32_t offset = difftime(mk_gmtime(&new), mk_gmtime(&current_time));
    time_t tmp_time;
    char str[25];
    asctime_r(&new, str);

    usart_print_P(PSTR("Updating time to: "));
    usart_println(str);

    rtc_set(&new);

    // Log time
    tmp_time = mk_gmtime(&log_last_time) + offset;
    gmtime_r(&tmp_time, &log_last_time);

    // Pump time
    tmp_time = mk_gmtime(&pump_last_time) + offset;
    gmtime_r(&tmp_time, &pump_last_time);

    // LCD time
    set_lcd_enabled(true);
}


/*
 * Respond to the user choosing new settings via the menu.
 */
void menu_edit_settings_callback(Settings new)
{
    const LogPeriod prev_period = settings.log_period;

    settings = new;
    update_settings_to_eeprom(&settings);

    if (settings.log_period != prev_period) {
        log_last_time = current_time;
    }
}


/*
 * Respond to the user choosing to execute some action via the menu.
 */
void menu_function_dispatch(MenuMode menu)
{
    switch (menu) {
        case START_PUMP:
            start_pump();
            break;
        case TOGGLE_LAMP:
            lamp_override = true;
            lamp_override_on = !pinout_is_set(pin_lamp);
            toggle_lamp();
            break;
        default:
            // noop
            break;
    }
}


/*
 * Display the plant's vital statistics on the screen.
 */
void show_status_on_lcd()
{
    char line[16];

    sensors_to_s(line, ring_buff_8_avg(&moisture),
            ring_buff_8_avg(&humidity),
            ring_buff_8_avg(&temperature));
    lcd_buffer_update(&lcd, 0, line);

    char lamp_icon = pinout_is_set(pin_lamp) ? LCD_CAPITAL_OMEGA : ' ';
    lcd_buffer_send_at(&lcd, 0, 15, lamp_icon);

    if (buoy_state == BUOY_UP) {
        lcd_show_time(&lcd, 1, current_time);
    } else {
        lcd_buffer_update_P(&lcd, 1, PSTR("\xBC\xBC Water Low! \xBB\xBB"));
    }
}


void sd_set_file_date_time(uint16_t* date, uint16_t* time)
{
    const time_t tz_time = mk_gmtime(&current_time) - SD_TIMEZONE_OFFSET;
    struct tm ftime;
    gmtime_r(&tz_time, &ftime);

    *date = FAT_DATE(ftime.tm_year + 1900, ftime.tm_mon, ftime.tm_mday);
    *time = FAT_TIME(ftime.tm_hour, ftime.tm_min, ftime.tm_sec);
}


/*
 * Respond to changes in the water level.
 */
void on_water_level_change(BuoyLevel level)
{
    if (level == BUOY_UP) {
        if (buzzer_is_on) {
            buzzer_set_enabled(false);
        }
    } else {
        // No water!
        set_lcd_enabled(true);
        buzzer_set_enabled(true);
    }
}


/*
 * Normally the LCD component uses 4 or 8 pins to drive its data. To conserve
 * pins on the microcontroller, we use a 2-wire shift register to drive those 4
 * pins.
 */
void shift_lcd_write4(__attribute__((unused)) const Lcd* lcd,
                      const uint8_t nibble)
{
    for (uint8_t i = 0; i < 4; ++i) {
        if ((nibble << i) & 0x08) {
            pinout_set(pin_lcd_data);
        } else {
            pinout_clr(pin_lcd_data);
        }
        pinout_set(pin_lcd_clk);
        pinout_clr(pin_lcd_clk);
    }
}


/*
 * Turn the LCD screen on or off and adjust the LCD timeout accordingly.
 */
void set_lcd_enabled(const bool enabled)
{
    if (enabled) {
        // updates screen timeout
        time_t timeout_at = mk_gmtime(&current_time) + SCREEN_TIMEOUT;
        gmtime_r(&timeout_at, &lcd_timeout_at);

        if (lcd_is_on) {
            return;
        }
        lcd_is_on = true;

        pinout_set(pin_lcd_backlight);
        lcd_display(&lcd, true);
    } else {
        if (!lcd_is_on) {
            return;
        }
        lcd_is_on = false;
        pinout_clr(pin_lcd_backlight);
        lcd_display(&lcd, false);
    }
}


/*
 * Turn the lamp on or off and update the lamp log file.
 */
void set_lamp_enabled(const bool enabled)
{
    if (pinout_is_set(pin_lamp) == enabled) {
        return;
    }

    if (enabled) {
        pinout_set(pin_lamp);
    } else {
        pinout_clr(pin_lamp);
    }
    if (sd_card_available) {
        log_lamp(&log_dir, current_time, enabled);
    }
}


/*
 * Alert the user of some kind of error condition with the buzzer and a message
 * on the LCD that cannot be dismissed without power-cycling.
 */
void fatal_error_P(const char* lcd0, const char* lcd1)
{
    fatal_error_active = true;
    buzzer_set_enabled(true);
    strncpy_P(fatal_error_lcd0, lcd0, 16);
    strncpy_P(fatal_error_lcd1, lcd1, 16);
}


/*
 * Check if it is time to write to the periodic log file and do so.
 */
void check_log()
{
    const struct tm next_time =
        log_next_time(log_last_time, settings.log_period);
    const int32_t time_left = difftime(mk_gmtime(&next_time),
            mk_gmtime(&current_time));

    if (time_left < 0) {
        log_last_time = current_time;

        log_status(&log_dir, current_time, &settings,
                ring_buff_8_avg(&moisture), ring_buff_8_avg(&humidity),
                ring_buff_8_avg(&temperature), buoy_state,
                pinout_is_set(pin_lamp), pump_last_time);
    }
}

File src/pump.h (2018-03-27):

#ifndef PUMP_H
#define PUMP_H
/* @file
 *
 *  "Planter" is a device that control a houseplant's water and light schedules.
 *  Copyright (C) 2018  Jon Sangster
 *
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
 *  You should have received a copy of the GNU General Public License along
 *  with this program.  If not, see <https://www.gnu.org/licenses/>.
 */

#include <stdbool.h>
#include <time.h>
#include <sangster/pinout.h>
#include <sangster/timer0.h>
#include <sangster/usart_p.h>

#include "sensors.h"
#include "settings.h"

/**
 * If the flow sensor doesn't detect any water moving after this many
 * milliseconds, it probably has become unplugged somehow
 */
#define PUMP_UNPLUGGED_CHECK_DELAY  2000

/**
 * The YF-S402 flow sensor returns a frequency 73 times times greater than the
 * flow rate, in L/min.
 */
#define YF_S402_FREQUENCY_FACTOR    73.0

/** Sentinel value returned by pump_check() when it's still pumping */
#define PUMP_STATUS_PUMPING         -1

/** Sentinel value returned by pump_check() when the sensor is unplugged */
#define PUMP_STATUS_UNPLUGGED       -2


/** Used to count the current flow sensor frequency */
volatile uint8_t pump_count;

/** The total water pumped so far, during this watering action */
double pump_total_ul;

/** The timer0 counter when the pump started */
uint16_t pump_started_at;

/** The date/time when the plant was last watered */
extern struct tm pump_last_time;


/**
 * @param [in] pin  The pin the pump is connected to
 */
void pump_start(const Pinout);

/**
 * Check if the pump should be stopped because it has already pumped enough
 * water.
 *
 * @return The total mL pumped. `-1` if the pump is still going or `-2` if it
 *   is unplugged
 * @note This function should be called on each main application loop.
 */
int16_t pump_check(Pinout, const Settings*, BuoyLevel);


/**
 * Increments the frequency counter when a signal is received from the sensor.
 *
 * @note Should be called in response to INT0_vect or INT1_vect, depending on
 *   which pin the sensor is connected to.
 */
__attribute__((always_inline))
static inline void pump_flow_callback()
{
    ++pump_count;
}


/** Reset the pump in preperation of another pump action */
__attribute__((always_inline))
static inline void pump_reset()
{
    pump_count = 0;
    pump_total_ul = 0;
}

#endif//PUMP_H

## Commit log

2018-03-27 Initial Planter Project features.
    - Add buzzer to Planter
    - Automatically start/stop lamp
    - Add Lamp/Pump menu functions
    - Speed check cycle to 250 ms
    - Archive toner transfers
    - Add logging
    - Add GPL License to plant project
    [Power Water.fzz, assembly.scad, box-assembly.scad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]
2018-03-27 Move code to src dir
    [Power Water.fzz, assembly.scad, box-assembly.scad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]
